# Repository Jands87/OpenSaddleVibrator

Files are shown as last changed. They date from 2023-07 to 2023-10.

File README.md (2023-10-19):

Note: This repository is still in progress.

The Open Saddle Vibrator is a sit-on vibrator that can be made at home with a 3D printer and some basic hand tools. The project is primarily made from timber, 3D printed parts and some metal angle iron.

Dome has an 7 ply ply-wood arch frames to keep its shape and is covered in 2 lays of 3 ply ply-wood with layers of thin rubber, foam and leather. It is also covered internally with a sound dampening material.

Base is 12mm ply wood to which the internal framework is bolted.

Sides are also 12mm plywood, covered in leather for aesthetics and have eyebolts mounted in the lower corners, handles and the IO and power connectors mounted.

The 3D framework is a strong square frame design connected parallel bars. On top of of the parallel bars is mounted 2 x M8 pillow block bearings holding a M8 steel shaft, which is pushed through an offset 3D printed shaft, this shaft is mounted to a pare of M12 pillow block bearings mounted to one end of the vibration plate. The other end of the of the vibration plate is connected to the parallel bars, via a 3D printed bride and a 20mm rubber dampener.

The electronics are relatively simple. An Arduino Uno acts as the mainboard, and an Arduino Nano acts as the controller.

The Uno as the mainboard controls the 2 ESCs controlling the rotation motor (55RPM 12V geared) and the vibration motor (100W 2750RPM straight motor).

The Nano in the controller has 2 pots to control the speed of the motor controllers and 2 buttons for the instant 100% pulse mode and the other for a slow ramping mode. The Arduinos communicate via serial using Serial.print() Arduino fuction with a very straight forward protocol (hoping to get it to use the buttplug.io system in the future).

You can find a great build guide over on the the OSV subreddit https://www.reddit.com/r/OpenSaddleVibrator written by u/stumro.

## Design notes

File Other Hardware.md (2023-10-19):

| Description | Qty Req |
|---|---|
|Nylon Rod and Spring Pack | 1 |
|Wild West 4" Silicone Attachment | 1 |

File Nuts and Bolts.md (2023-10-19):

|Size| Where is it used | Qty Req |
|---|---|---|
|M5x16 | M8 Bearing to M8 Bearing Mount	|4|
|M6x16 | M15 Bearing to M15 Bearing Mount	|4|
|M6x16 | Toy Plate to Toy Mount Post	|2|
|M6x20 | Toy Holder to Toy Mount Post	|2|
|M6x20 | Toy Plate to M15 Bearing Mount	|4|
|M6x20 | Rotary Motor Bearing Clasp to Motor Motor Block	|2|
|M6x25 | Rotary Motor Block to Rotary Motor Motor Clasp	|4|
|M6x25 | Frame Rail to M8 Bearing Mount	|4|
|M6x25 | Frame Rail to Frame Legs	|8|
|M6x25 | Frame Rail to Support Bridge	|4|
|M6x35 | 100W Motor Clamp to 100W Motor Mount	|4|
|M8x20 | Rotary Motor Mount to Rotary Motor Block	|2|
|M5 | Nuts (For M8 Bearing)	|4|
|M6 | Nuts (For M15 Bearing)	|4|
|M6x35 | Frame Legs to Base (x8) (Countersunk)	|8|
|M8x30 | 100W Motor Mount to Base (x2) (Countersunk)	|2|
|M8x30 | Rotary Motor Mount to Base (x2) (Countersunk)	|2|
|M8x80 Rod | Not needed for single frame rail print	|2|
|M8x150 | M8 Bearing through Bearing Offset	|1|
<h6>Nylon Rod and Spring Pack x 1 </h6>

<br>

<h2>Wild West 4" Silicone Attachment x 1

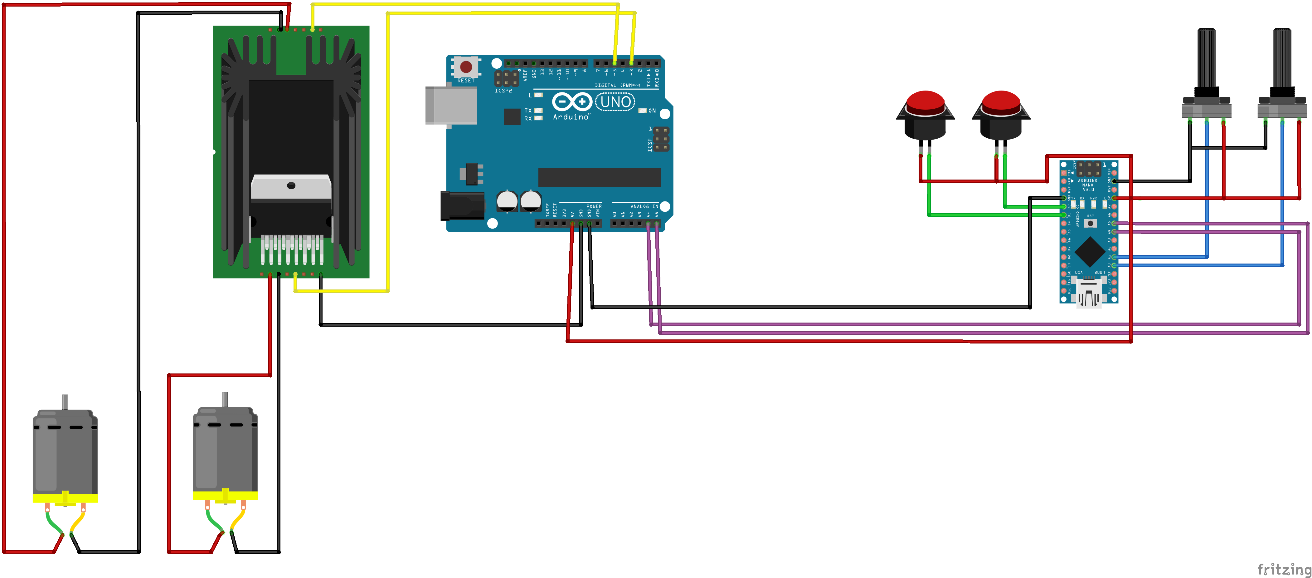
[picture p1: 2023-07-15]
images/schematic.png

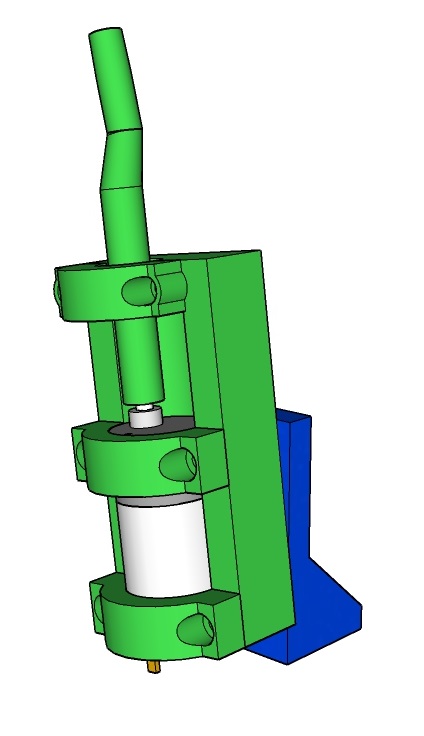
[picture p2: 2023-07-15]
design_files/Rotary Motor/Rotary Motor.jpg

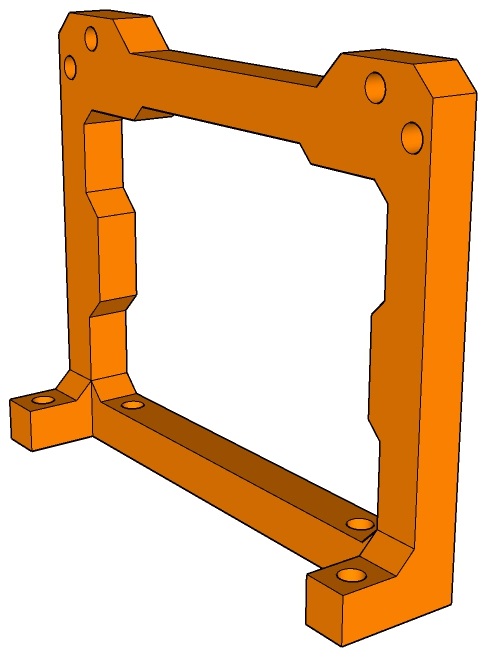
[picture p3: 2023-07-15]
design_files/Frame Leg/Frame Leg.jpg

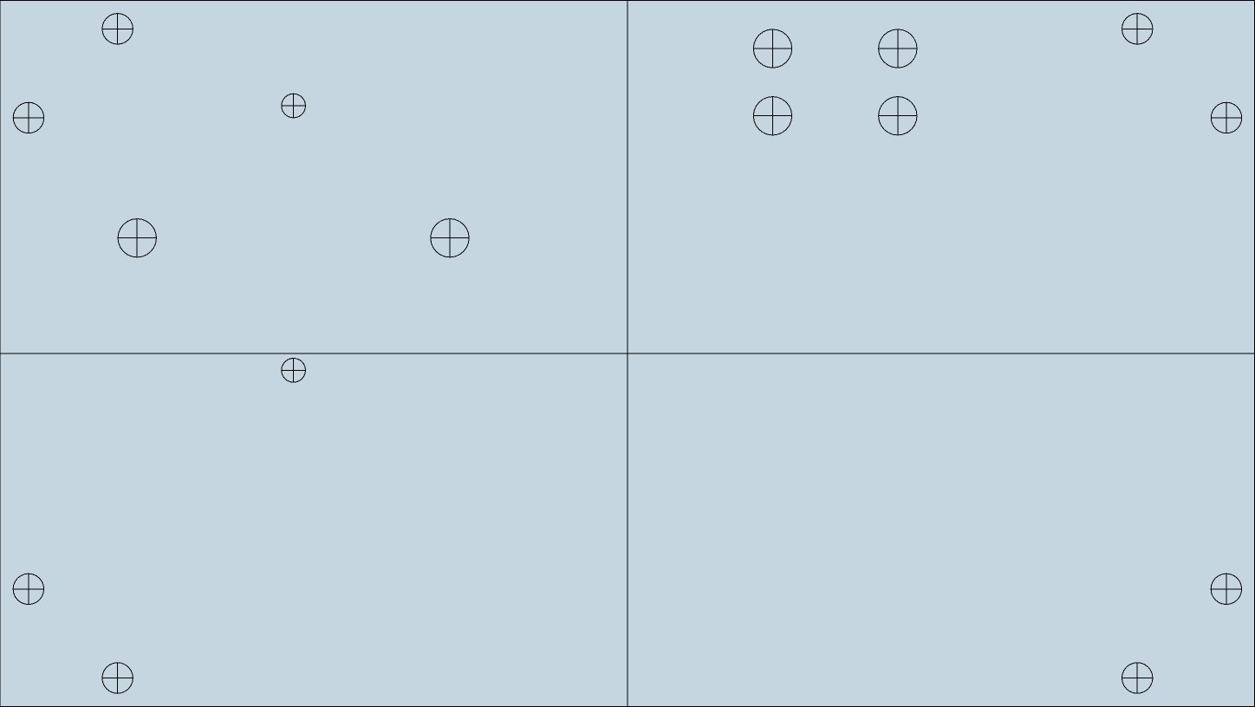
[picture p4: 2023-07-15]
design_files/Base/Base Template.jpg

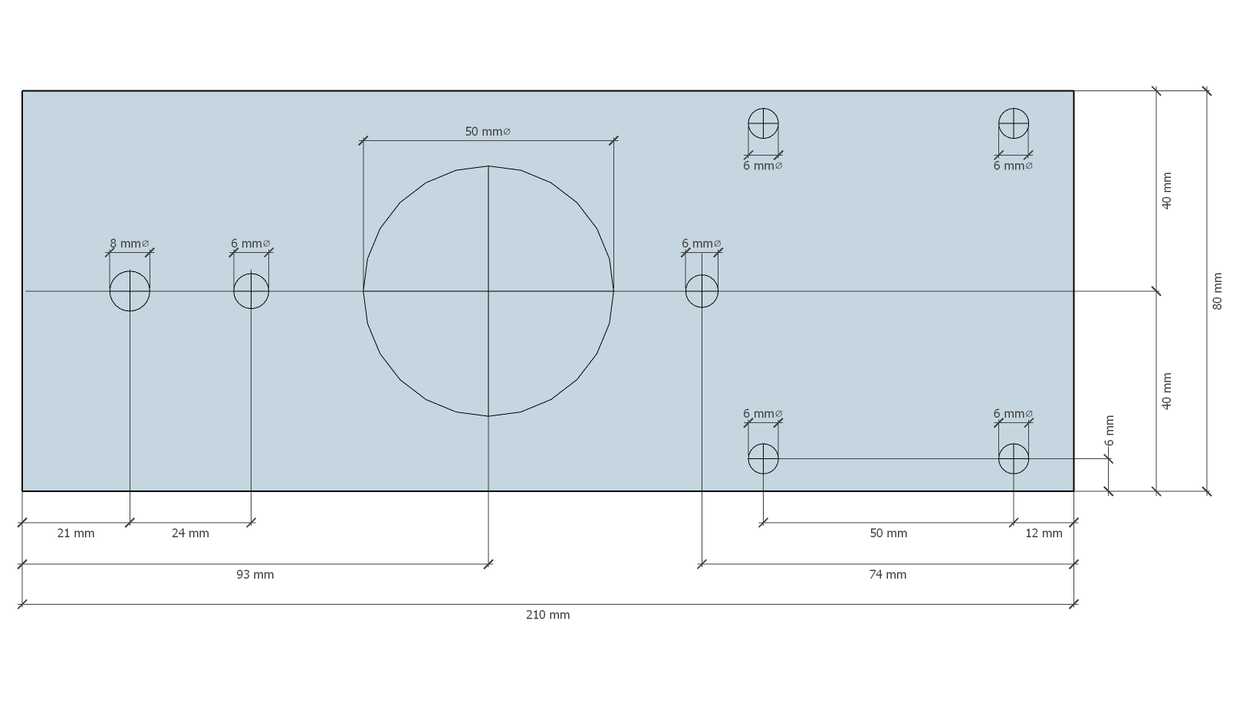
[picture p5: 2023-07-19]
design_files/Toy Plate/Toy Plate Template.png

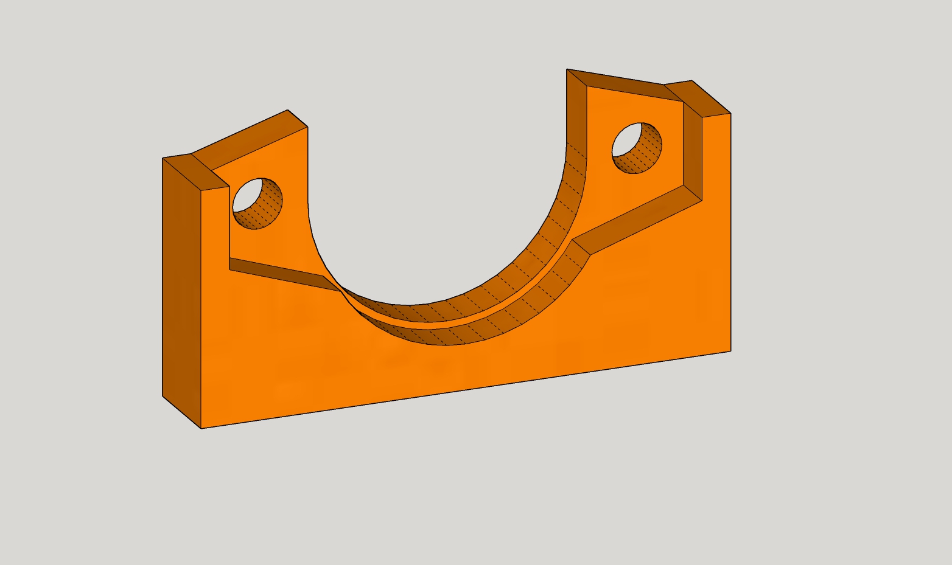
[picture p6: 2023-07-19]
design_files/M15 Bearing/M15 Bearing Mount.jpg

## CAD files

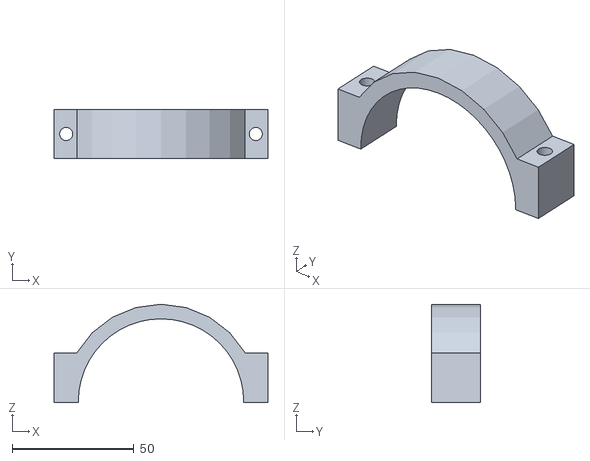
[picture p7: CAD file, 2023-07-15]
design_files/100W Motor/100W Motor Mount - Clamp.stl
88.0 x 20.0 x 40.5

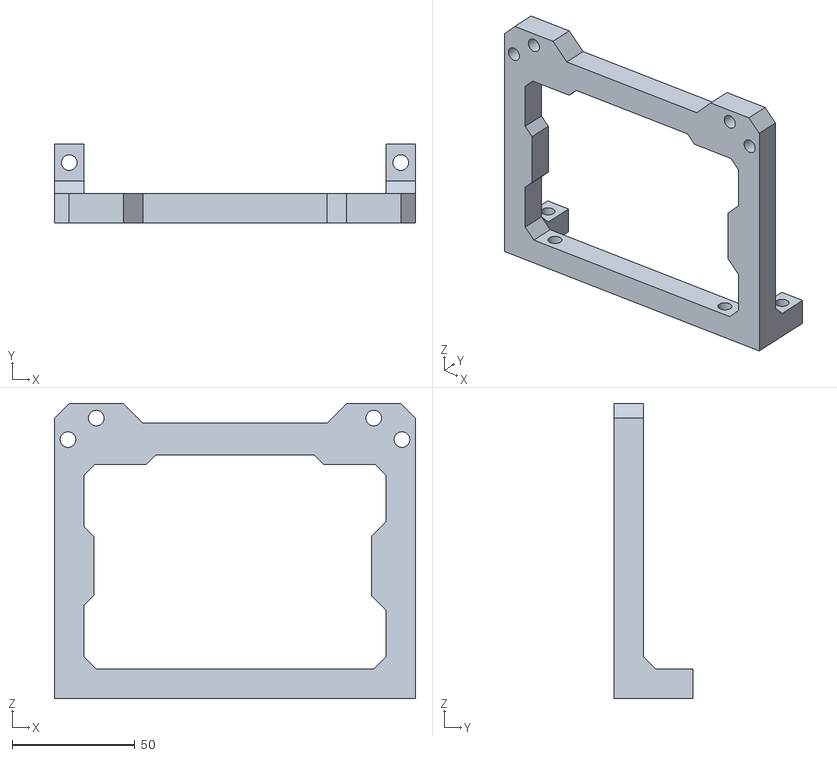
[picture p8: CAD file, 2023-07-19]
design_files/Frame Leg/Frame Leg.stl
147.0 x 32.0 x 120.2

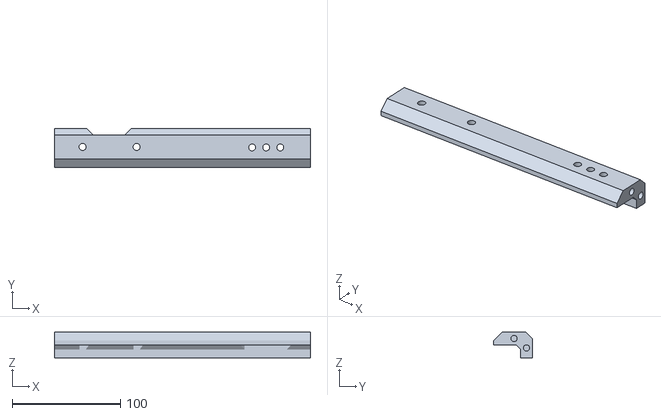
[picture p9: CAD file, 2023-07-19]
design_files/Frame Rails/Frame Rails - 2 Single Print.stl
237.0 x 36.0 x 24.0

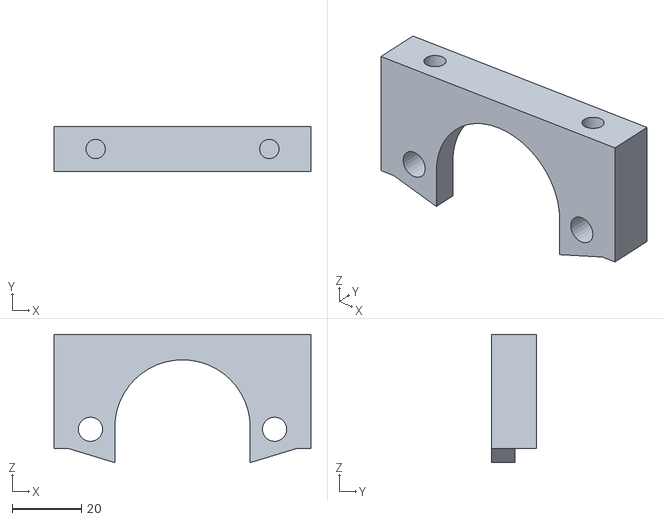
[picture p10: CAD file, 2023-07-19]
design_files/M15 Bearing/M15 Bearing Mount.stl
74.0 x 12.9 x 36.9

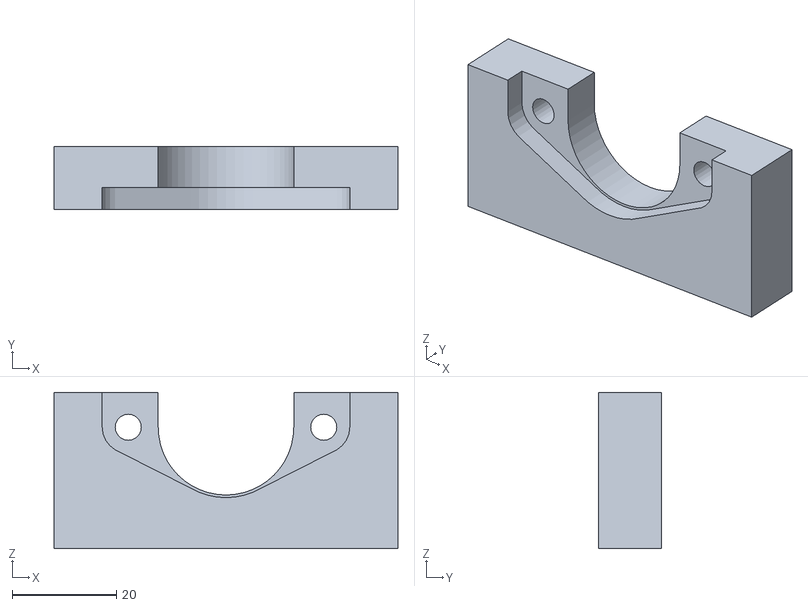
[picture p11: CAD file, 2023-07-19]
design_files/M8 Bearing Mount/M8 Bearing Mount.stl
66.0 x 12.0 x 30.0

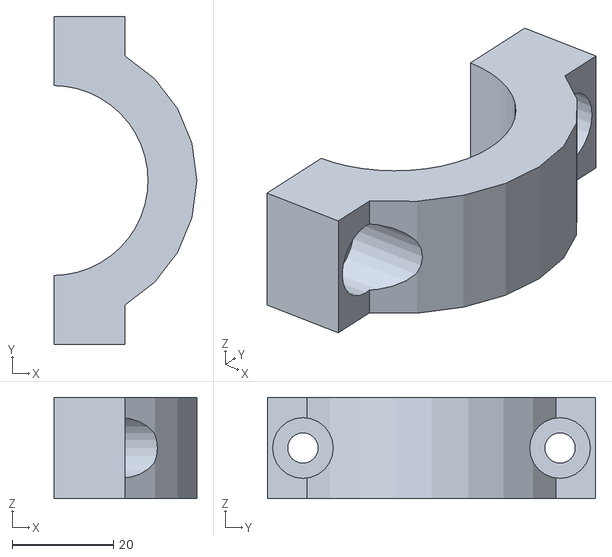
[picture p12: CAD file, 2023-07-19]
design_files/Rotary Motor/Rotary Motor Motor Clasp.stl
28.2 x 64.8 x 20.0

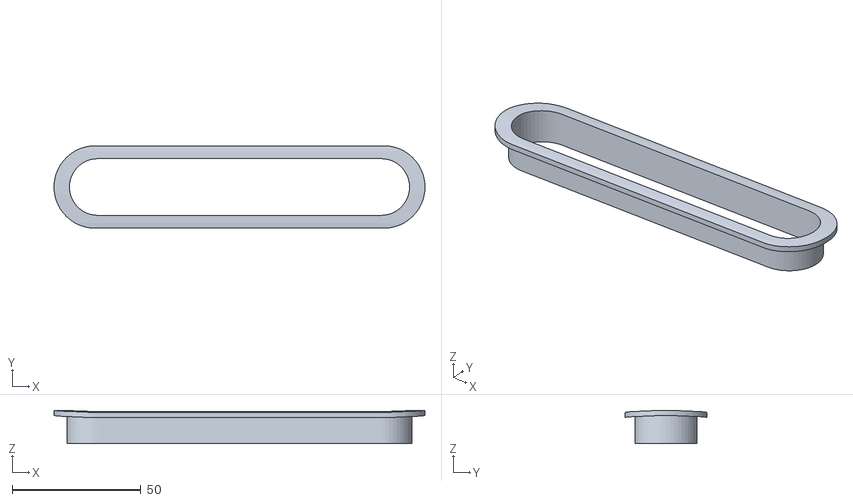
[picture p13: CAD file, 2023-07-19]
design_files/Shell Insert/shell insert.stl
144.0 x 32.0 x 12.9

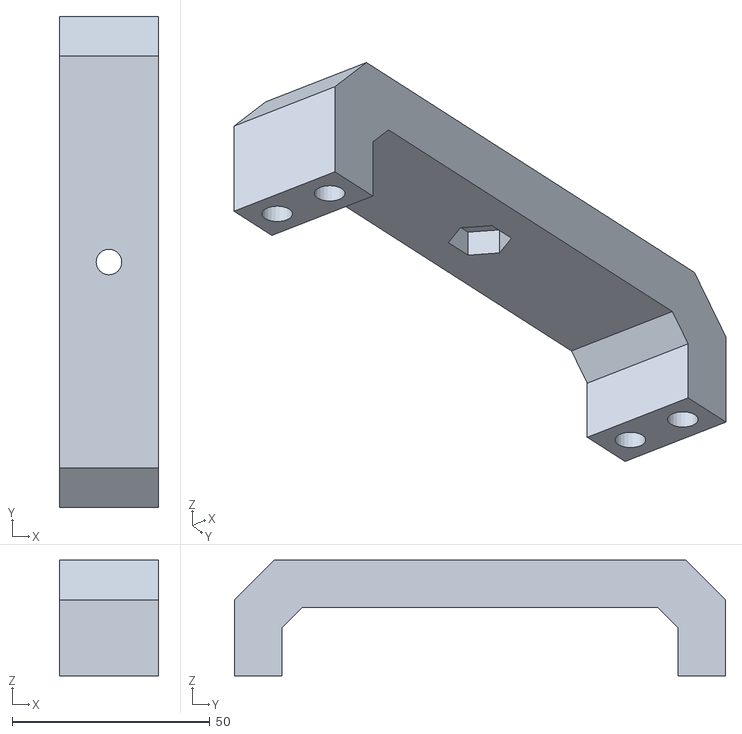
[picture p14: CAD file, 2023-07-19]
design_files/Support Bridge/Support Bridge.stl
25.0 x 124.0 x 29.2

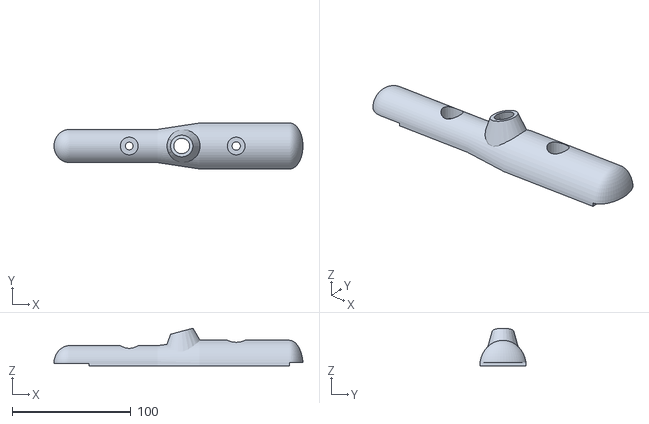
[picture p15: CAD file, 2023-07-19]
design_files/Toy Mount/Toy Mount_1_Piece.stl
209.5 x 38.7 x 31.6

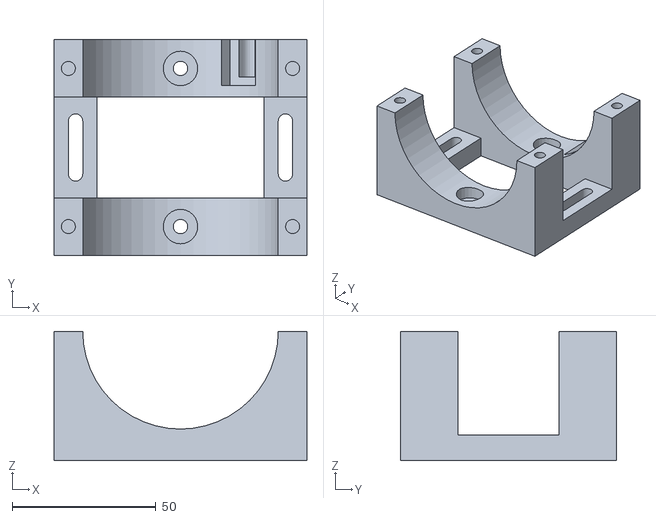
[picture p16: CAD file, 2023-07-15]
design_files/100W Motor/100W Motor Mount - Base.stl
88.0 x 75.0 x 45.0

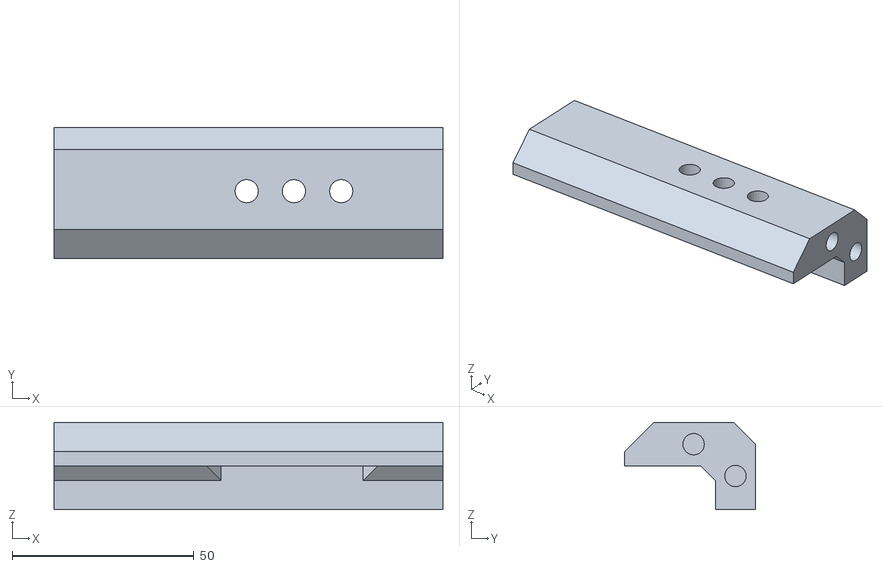
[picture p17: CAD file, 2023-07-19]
design_files/Frame Rails/Frame Rails - 2.stl
107.0 x 36.0 x 24.0

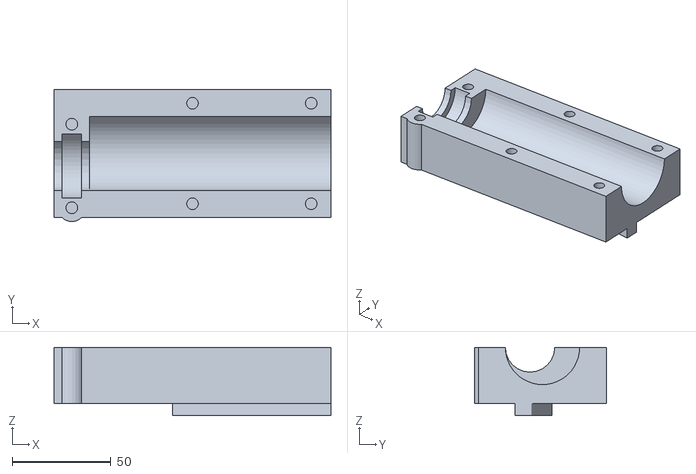
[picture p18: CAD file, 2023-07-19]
design_files/Rotary Motor/Rotary Motor Block.stl
140.0 x 66.8 x 34.4

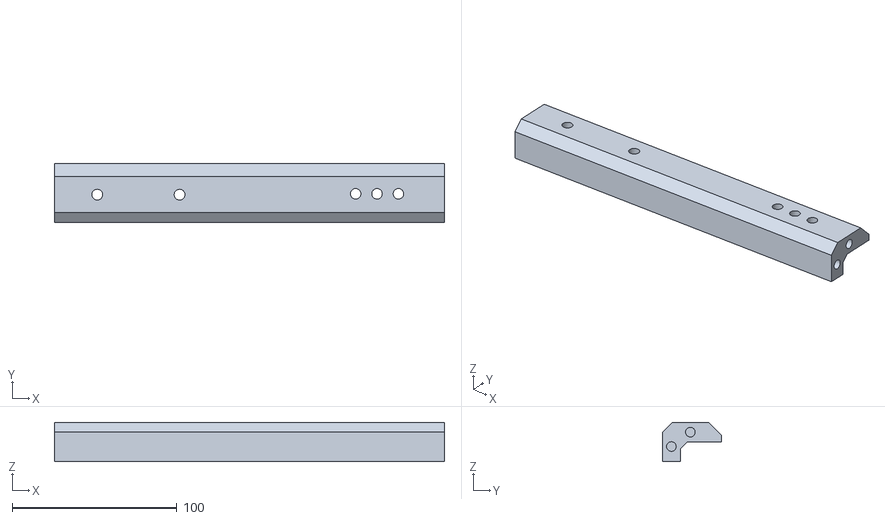
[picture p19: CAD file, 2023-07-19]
design_files/Frame Rails/Frame Rails - 1 Single Print.stl
237.0 x 36.0 x 24.0

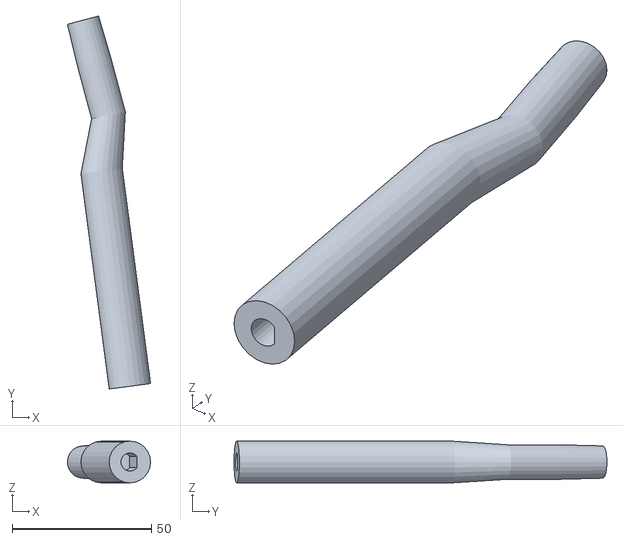
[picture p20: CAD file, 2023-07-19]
design_files/Rotary Motor/Rotary Motor Post.stl
29.9 x 133.9 x 15.0

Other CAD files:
design_files/Toy Mount/Toy Mount AIO.stl
design_files/Toy Mount/Toy Mount Post.stl
design_files/Frame Rails/Frame Rails - 3.stl
design_files/Rotary Motor/Rotary Motor Mount.stl
design_files/Base/Base Template.skp
design_files/Frame Leg/Frame Leg.skp
design_files/Frame Rails/Frame Rails - 1.stl
design_files/Frame Rails/Frame Rails - 4.stl
design_files/Frame Rails/Frame Rails.skp
design_files/M15 Bearing/M15 Bearing Mount.skp
design_files/M8 Bearing Mount/M8 Bearing Mount.skp
design_files/Open Saddle Vibrator.skp
design_files/Rotary Motor/Rotary Motor Bearing Clasp.stl
design_files/Rotary Motor/Rotary Motor Mount.skp
design_files/Rotary Motor/Rotary Motor Post.skp
design_files/Shell Insert/shell insert.skp
design_files/Support Bridge/Support Bridge.skp
design_files/Toy Mount/Toy Mount AIO.skp
design_files/Toy Mount/Toy Mount Post.skp
design_files/Toy Mount/Toy Mount.skp
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

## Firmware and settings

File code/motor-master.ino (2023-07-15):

// Master code for Arduino Uno for the Saddle Vibrator
// https://www.thingiverse.com/thing:3554455
// Version 1.0 (14.4.19)

#include <Wire.h>

byte inData[10];                                 // incomming data array for data from controller (make larger than you need)

const int  motor0 = 3;                           // pin designation for motor 0
const int  motor1 = 5;                           // pin designation for motor 1
const int  LED = 13;                             // LED showing debugging mode

bool  button0 = 0;                               // internal variables for button 0 on controller
bool  button1 = 0;
bool  button1flag = 0;                           // check flag to see if button is being held down, debounce
bool  rampmode = 0;                              // flag for ramping mode on motor 0
bool  flag = 0;                                  // dead man switch for connection, stop motors if no data
bool  debugflag = 0;                             // set 1 for debugflag mode to print serial updates

void setup()
{
  delay(500);                                    // allow controller to start first
  Wire.begin();                                  // join i2c bus (address optional for master)
  Serial.begin(9600);                            // set serial baud to 9600
}

void loop() {

  flag = 0;                                      // set connection flag to off to show data to stop motors if no data arrives
  Wire.requestFrom(8, 5);                        // request 5 bytes from slave device #8
  while (Wire.available()) {
    for (int i = 0; i <= 4; i++) {
      inData[i] = Wire.read(); - '0';            // read 1 byte from the wire buffer in to "inData[i]"  -'0' is to convert back to int from char  
    }
    button0 = inData[2];                         // check to see if any buttons have been presed
    button1 = inData[3];
    
    if (inData [4] == 1){
      debugflag = 1;                             // enter debug mode
      digitalWrite(LED, HIGH);                   // LED showing debugging mode, HIGH);
    }
    else
    {
      debugflag = 0;                             // exit debug mode
      digitalWrite(LED, LOW);                    // LED showing debugging mode, HIGH);
    }
    
    flag = 1;                                    // set connection flag to on to show data has arrived.
  }

  if (flag == 0) {                               // deadman (no connection) switch to stop motors
    for (int i = inData[0]; i == 0; i--) {       // decrease motor 0 and 1 speeds until stopped
      analogWrite(motor0, 0);
      delay(10);
    }
    for (int i = inData[1]; i == 0; i--) {
      analogWrite(motor1, 0);
      delay(10);
    }
  }


  if (flag == 1) {                                // only continue if controller is connected (deadman switch check)

    // ***************** BUTTON 0 ROUTINES *****************

    if (button0 == 1) {                           // process button routine if button0 has been pressed
      button0press();
    }

    // ***************** BUTTON 1 ROUTINES *****************

    if (button1 == 1) {                           
      button1flag = 1;                            // set button flag to make sure it does not continuously run the routine (debounce)
    }

    if ((button1 == 0) && (button1flag == 1)) {   // if button has been released reset button0 flag and process routine
      button1flag = 0;
      if (rampmode == 0) {
        button1press();
      }
      else if (rampmode == 1) {
        rampmode = 0;
      }

    }

    // ****************** MOTOR  ROUTINES ******************

    if ((button0 == 0) && (button1 == 0)) {       // no buttons have been pressed - set motor speed
      if (rampmode == 1) {
        inData[0] = 255;
      }
      analogWrite(motor0, inData[0]);           // PWM to output motor 0 port
      delay(10);
      analogWrite(motor1, inData[1]);             // PWM to output motor 1 port
    }
  }
  if (debugflag == 1) {
    showSerial();
    delay(1000);
  }
  else if (debugflag == 0) {
    delay(100);
  }
}

void button0press() {                             // button0 has been pressed
  inData[0] = 255;                                // set motor0 speed to 100%
  analogWrite(motor0, inData[0]);                 // PWM to output motor 0 port
}

void button1press() {                             // button1 button has been pressed
  rampmode = 1;
  for (int i = inData[0]; i <= 255; i++) {            // slowly ramp motor speed to 100%
    Serial.print(i);
    Serial.println(".");
    analogWrite(motor0, i);
    delay(10);
  }
  Serial.println();
}

void showSerial() {
  Serial.print("Masterboard Status: ");
  if (flag == 0) {                                // deadman (no connection) switch to stop motors
    Serial.println("Controller disconnected. (Debugging)");
  }
  else if (flag == 1) {
    Serial.println("Controller connected. (Debugging)");
  }
  Serial.print("Motor 0:");
  Serial.print(inData[0]);
  Serial.print(" / ");
  Serial.print("Motor 1:");
  Serial.print(inData[1]);
  Serial.print(" / ");
  Serial.print("Button 0:");
  Serial.print(button0);
  Serial.print(" / ");
  Serial.print("Button 1:");
  Serial.print(button1);
  Serial.print(" / ");
  Serial.print("Button 1 Flag:");
  Serial.print(button1flag);
  Serial.print(" / ");
  Serial.print("Ramp Mode:");
  Serial.print(rampmode);

  Serial.println();
  Serial.println();
}

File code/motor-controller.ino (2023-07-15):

// Master code for Arduino Uno for the Saddle Vibrator by Jands
// https://www.thingiverse.com/thing:3554455
// Version 1.0 (14.4.19)

#include <Wire.h>

const int pot0 = A0;              // pin designation for pot 0
const int pot1 = A1;              // pin designation for pot 1
const int butt0 = 2;              // pin designation for button 0
const int butt1 = 3;              // pin designation for button 1
const int  LED = 13;              // LED showing debugging mode

byte motor0;
byte motor1;
byte button0;
byte button1;
byte debugflag;

void setup()
{
  Wire.begin(8);                  // join i2c bus with address #8
  Wire.onRequest(requestEvent);   // register event

  Serial.begin(9600);             // set serial baud to 9600
  Serial.println("Slave");        // print on screen position of board

  pinMode(butt0, INPUT_PULLUP);   // set both inputs to internal pull ups
  pinMode(butt1, INPUT_PULLUP);
}

void loop()
{
  motor0 = map(analogRead(pot0), 0, 1023, 0, 255);  // map will return byte size data
  delay(10);
  motor1 = map(analogRead(pot1), 0, 1023, 0, 255);
  button0 = !digitalRead(butt0);                    // read in button status and invert
  button1 = !digitalRead(butt1);
  delay(100);                      // 0.1-sec interval as a test interval

  if ((digitalRead(butt0) == 0) && (digitalRead(butt1) == 0)) {   // enter debug mode if both buttons pressed when powered on
    if (debugflag == 0) {
      debugflag = 1;
      digitalWrite(LED, HIGH);
      button0 = 0;
      button1 = 0;
      delay(1000);
    }
    else {
      debugflag = 0;
      digitalWrite(LED, LOW);
      button0 = 0;
      button1 = 0;
      delay(1000);
    }
  }
}

void requestEvent()
{
  Wire.write(motor0);              // data item-1 as ASCII codes
  Wire.write(motor1);              // data item-2 as ASCII codes
  Wire.write(button0);             // data item-3 as ASCII codes
  Wire.write(button1);             // data item-3 as ASCII codes
  Wire.write(debugflag);           // data item-3 as ASCII codes

  if (debugflag == 1) {
    Serial.print(motor0);            // data item-1 as ASCII codes
    Serial.print(",");               // local seperator
    Serial.print(motor1);            // data item-2 as ASCII codes
    Serial.print(",");               // local seperator
    Serial.print(button0);           // data item-3 as ASCII codes
    Serial.print(",");               // local seperator
    Serial.print(button1);           // data item-3 as ASCII codes
    Serial.print(",");               // local seperator
    Serial.println(debugflag);       // display debug status
  }
}

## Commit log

2023-07-15 100W motor mount design file upload
    [100W Motor Mount - Base.stl, 100W Motor Mount - Clamp.stl]
2023-07-15 Base plate design file upload
2023-07-19 Frame leg design file upload
    [Frame Leg.stl]
2023-07-19 Frame rail design file upload
    Print either 1 each of the 'Single Print' stl files, or print the 1-4 stl files.'.
    [Frame Rails - 1 Single Print.stl, Frame Rails - 1.stl, Frame Rails - 2 Single Print.stl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]
2023-07-19 M8 bearing mount design file upload
    [M8 Bearing Mount.stl]
2023-07-19 M15 bearing mount design file upload
    [M15 Bearing Mount.stl]
2023-07-19 Rotary motor mount design file upload
    [Rotary Motor Bearing Clasp.stl, Rotary Motor Block.stl, Rotary Motor Motor Clasp.stl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]
2023-07-19 Parts design file upload
    [Support Bridge.skp, Support Bridge.stl, Toy Mount AIO.skp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]
2023-07-19 Vibration plate design file upload
    [Toy Plate.skp]
2023-10-19 Update and rename parts_list.md to Nuts and Bolts.md
